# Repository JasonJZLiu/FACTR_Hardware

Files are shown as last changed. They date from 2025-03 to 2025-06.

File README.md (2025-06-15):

<h1> FACTR Low-Cost Force-Feedback Teleoperation Hardware</h1>

#### [Jason Jingzhou Liu](https://jasonjzliu.com)<sup>\*</sup>, [Yulong Li](https://yulongli42.github.io)<sup>\*</sup>, [Kenneth Shaw](https://kennyshaw.net), [Tony Tao](https://tony-tao.com), [Ruslan Salakhutdinov](https://www.cs.cmu.edu/~rsalakhu/), [Deepak Pathak](https://www.cs.cmu.edu/~dpathak/)
_Carnegie Mellon University_

[Project Page](https://jasonjzliu.com/factr/) | [arXiV](https://arxiv.org/abs/2502.17432) | [FACTR](https://github.com/RaindragonD/factr/) | [FACTR Teleop](https://github.com/RaindragonD/factr_teleop/)

<h1> </h1>
<div style="display: flex; gap: 10px; align-items: center;">
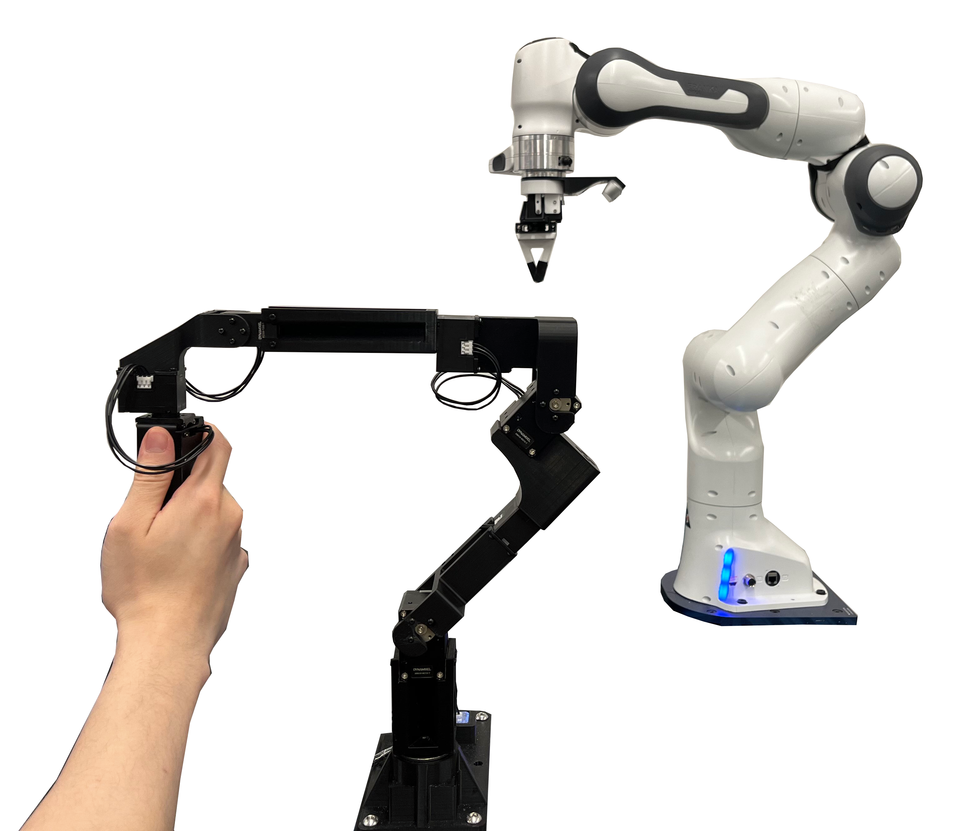
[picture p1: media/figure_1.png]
teaser_1
  
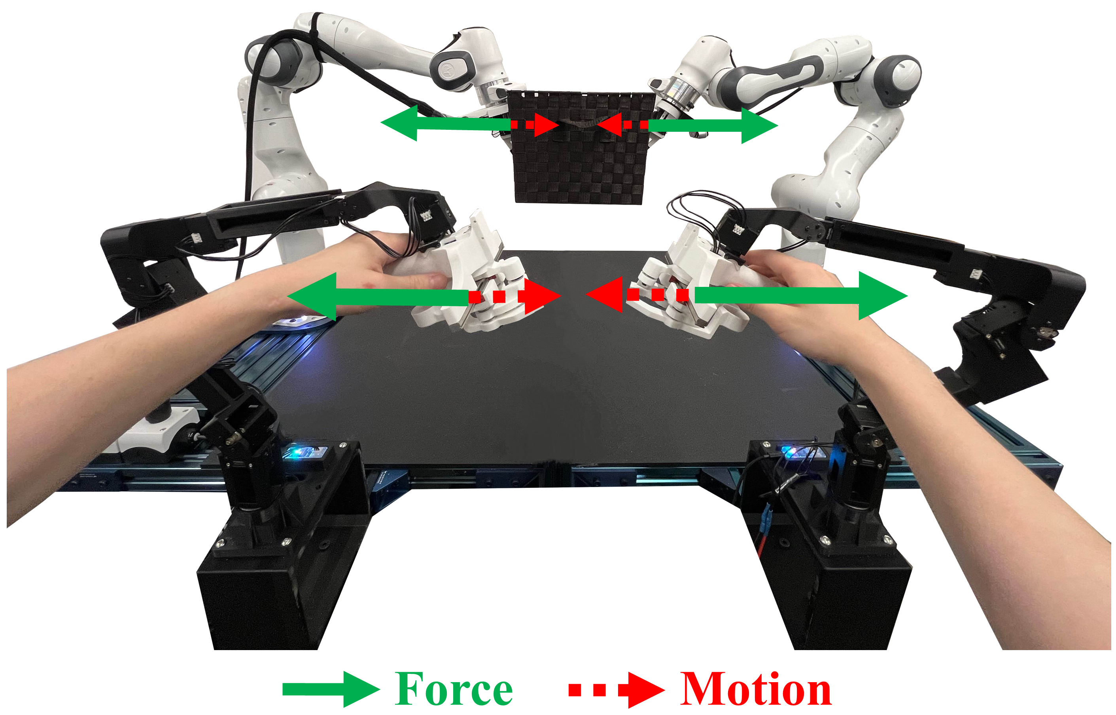
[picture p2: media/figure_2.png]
teaser_2
  
</div>

<br>

## Catalog
- [Bill of Materials](#bill-of-materials)
- [Building Instructions](#building-instructions)
- [License and Acknowledgements](#license-and-acknowledgements)
- [Citation](#citation)

## Bill of Materials
All costs are listed in USD.
<table>
  <thead>
    <tr>
      <th>Item</th>
      <th>Quantity</th>
      <th>Cost per Item</th>
      <th>Total Cost</th>
      <th>Note</th>
    </tr>
  </thead>
  <tbody>
    <tr>
      <td>Dynamixel XM430-W210-T Servo Motor</td>
      <td>2</td>
      <td>269.9</td>
      <td>539.8</td>
      <td><a href="https://www.robotis.us/dynamixel-xm430-w210-t/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">Purchase Link</a></td>
    </tr>
    <tr>
      <td>Dynamixel XC330-T288-T Servo Motor</td>
      <td>6</td>
      <td>89.9</td>
      <td>539.4</td>
      <td><a href="https://www.robotis.us/dynamixel-xc330-t288-t/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">Purchase Link</a></td>
    </tr>
    <tr>
      <td>U2D2 Control PCB</td>
      <td>1</td>
      <td>32.1</td>
      <td>32.1</td>
      <td><a href="https://www.robotis.us/u2d2/?srsltid=AfmBOopG82m7F47C2HJT4Q9btluaBp5lSfk2BS-57h5wBO3lwNoY3PoJ">Purchase Link</a></td>
    </tr>
    <tr>
      <td>12V 20A Power Supply</td>
      <td>1</td>
      <td>24.99</td>
      <td>24.99</td>
      <td><a href="https://www.amazon.com/ALITOVE-Transformer-Switching-Converter-Security/dp/B078RTV41D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">Purchase Link</a></td>
    </tr>
    <tr>
      <td>FPX330-S102 Servo Bracket</td>
      <td>1</td>
      <td>8.7</td>
      <td>8.7</td>
      <td><a href="https://www.robotis.us/fpx330-s102-4pcs-set/">Purchase Link</a></td>
    </tr>
    <tr>
      <td>Servo Idler for XM430 Servos</td>
      <td>2</td>
      <td>19.58</td>
      <td>39.16</td>
      <td><a href="https://www.robotis.us/hn12-i101-set/?srsltid=AfmBOooTVv1ehj551FepxB_NaPDrjRdgRIVPH26-N-vjoncqV3CZYdAC">Purchase Link</a></td>
    </tr>
    <tr>
      <td>Servo Idler for XC330 Servos</td>
      <td>1</td>
      <td>10.78</td>
      <td>10.78</td>
      <td><a href="https://www.robotis.us/fpx330-h101-4pcs-set/?srsltid=AfmBOopdWLnJLGadW4_-EK1PhWCb8sMwZvdChQUPqFrf1NNLNWeow4cJ">Purchase Link</a></td>
    </tr>
    <tr>
      <td>Polymaker PLA PRO Filament</td>
      <td>1</td>
      <td>24.99</td>
      <td>24.99</td>
      <td><a href="https://www.amazon.com/dp/B099KS2PDW?ref_=cm_sw_r_cp_ud_dp_9TYAHY4XBF45WRGQJGQ6">Purchase Link</a></td>
    </tr>
    <tr>
      <td>U2D2 Power Hub Board</td>
      <td>1</td>
      <td>19.99</td>
      <td>19.99</td>
      <td><a href="https://www.robotis.us/u2d2-power-hub-board-set/">Purchase Link</a></td>
    </tr>
    <tr>
      <td>14AWG Cable</td>
      <td>1</td>
      <td>23.99</td>
      <td>23.99</td>
      <td><a href="https://www.amazon.com/dp/B088RDY284?ref_=cm_sw_r_cp_ud_dp_4ESS07CK5QSXK185XQEP&th=1">Purchase Link</a></td>
    </tr>
    <tr>
      <td>3/4" Bearing</td>
      <td>1</td>
      <td>6.99</td>
      <td>6.99</td>
      <td><a href="https://www.amazon.com/4-Pack-Bearings-Carbon-Steel-Wheelbarrows/dp/B0CFDNP445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">Purchase Link</a></td>
    </tr>
    <tr>
      <td>M2.5×8mm</td>
      <td>8</td>
      <td>N/A</td>
      <td rowspan="3">15.99</td>
      <td rowspan="3"><a href="https://www.amazon.com/NINDEJIN-Replacement-Computer-Miniature-Motherboard/dp/B08KXS2MWG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">Purchase link</a></td>
    </tr>
    <tr>
      <td>M2×10mm</td>
      <td>20</td>
      <td>N/A</td>
    </tr>
    <tr>
      <td>M2×6mm</td>
      <td>14</td>
      <td>N/A</td>
    </tr>
    <tr>
      <td>M2×8mm (Self Tapping)</td>
      <td>24</td>
      <td>N/A</td>
      <td rowspan="2">0</td>
      <td rowspan="2">Comes with Dynamixel XC330-T288-T Servo Motor</td>
    </tr>
    <tr>
      <td>M2×6mm (Self Tapping)</td>
      <td>8</td>
      <td>N/A</td>
    </tr>
    <tr>
      <td>M2×4mm</td>
      <td>4</td>
      <td>N/A</td>
      <td>0</td>
      <td>Comes with FPX330-S102 Servo Bracket</td>
    </tr>
    <tr>
      <td colspan="3"><b>Total</b></td>
      <td colspan="2"><b>1279.89</b></td>
    </tr>
  </tbody>
</table>

## Building Instructions

### Screw Guide

The FACTR Teleoperation Franka Leader Arm assembly requires six types of screws:

- **Screw A**: M2.5 × 8 mm  
- **Screw B**: M2 × 10 mm  
- **Screw C**: M2 × 8 mm (Self-tapping)  
- **Screw D**: M2 × 6 mm (Self-tapping)  
- **Screw E**: M2 × 6 mm  
- **Screw F**: M2 × 4 mm  

**Note:**  
- Screws **C** and **D** are included with the *Dynamixel XC330-T288-T* servos.  
- Screw **F** is included with the *FPX330-S102* servo bracket.

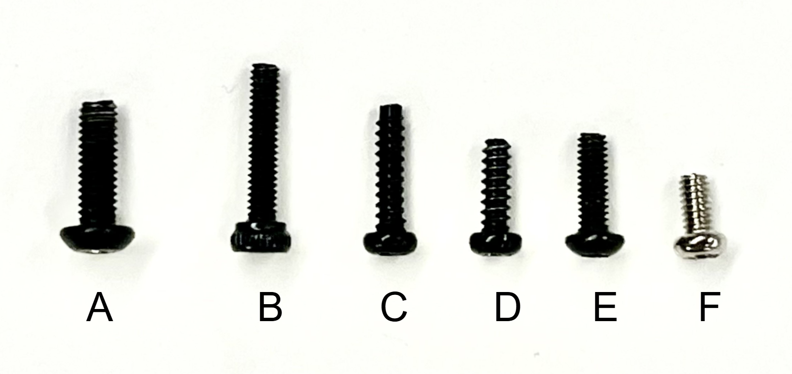
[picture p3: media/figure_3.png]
Screw Guide


---

### Step 1: Configure the Power Supply
- Connect the **12V Power Supply** to the **U2D2 Power Hub Board**.  
- Connect the **U2D2 Control PCB** to the **U2D2 Power Hub Board**.

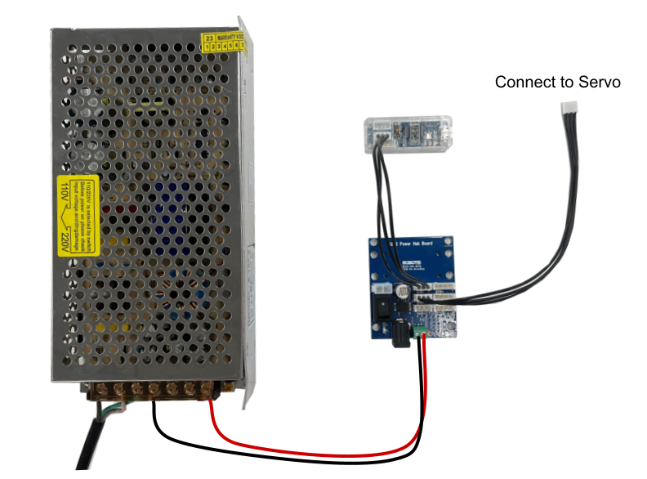
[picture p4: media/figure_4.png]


**Note:** Alternative ways of supplying power to the **U2D2 Control PCB** and the servos without using **U2D2 Power Hub Board** are available. 
Please refer to [here](https://emanual.robotis.com/docs/en/parts/interface/u2d2/) for more methods.

### Step 2: Update Servo IDs
By default, all Dynamixel servos are set to ID 1. To control multiple servos with a single U2D2 controller, 
each servo must be assigned a unique ID. This assignment should be done one servo at a time, starting with 
the servo closest to the robot base and progressing up the kinematic chain. Assign IDs sequentially from 
1 up to 8, with the gripper trigger servo holding ID 8. 

| Joint ID | Servo Type |
|---|---|
| 1 | Dynamixel XC330-T288-T |
| 2 | Dynamixel XM430-W210-T |
| 3 | Dynamixel XC330-T288-T |
| 4 | Dynamixel XM430-W210-T |
| 5 | Dynamixel XC330-T288-T |
| 6 | Dynamixel XC330-T288-T |
| 7 | Dynamixel XC330-T288-T |
| 8 | Dynamixel XC330-T288-T |

#### Steps to Change a Servo's ID:
1. **Connect a single servo to the U2D2 Power Hub Board.**
2. **Install and launch the [Dynamixel Wizard](https://emanual.robotis.com/docs/en/software/dynamixel/dynamixel_wizard2/) software.**
3. **Configure the scanning settings:**
   - In the top menu bar, go to **Tools → Options**.
   - Under **"Select port to scan"**, ensure all ports are selected.
   - Under **"Select baudrate to scan"**, choose the correct baudrate. The default is **57600 bps**. If unsure, select all available options.
   - Under **"Set ID range to scan"**, you can speed up scanning by limiting the range to **0–15**, unless the servo might already have an ID outside this range.
4. **Click the Scan icon** (magnifying glass with a gear) in the top-left corner.
   - If the servo is found, it will appear in the left panel of the window.
5. **Select the detected servo** from the panel, then click **ID** found in the middle panel of the window.
   - Select the new ID on the right panel of the window and click **Save**.
6. **Repeat** the above steps for each servo.

### Step 3: 3D Print the Body Links of the Leader Arm
The leader arm consists of **nine 3D-printed parts**. STL files for all components can be found in the `/3D_printing_files` directory.

- **Material**: PLA  
- **Infill**: 20%

To ensure accurate dynamic modeling, each printed part should closely match the specified mass values. These values correspond to the mass values 
defined in the provided URDF file. This URDF file is used to compute gravity compensation and other dynamics-related calculations.

The table below lists each part, its corresponding STL file, and its reference mass:

| Part Name | STL File | Mass (g) |
|---|---|---|
| Base Link | factr_teleop_franka_base.STL | 150 |
| Link 1 | factr_teleop_franka_l1.STL | 31 |
| Link 2 | factr_teleop_franka_l2.STL | 19 |
| Link 3 | factr_teleop_franka_l3.STL | 29 |
| Link 4 | factr_teleop_franka_l4.STL | 28 |
| Link 5 | factr_teleop_franka_l5.STL | 25 |
| Link 6 | factr_teleop_franka_l6.STL | 12 |
| Gripper Handle | factr_teleop_gripper_leader_handle.STL | 21 |
| Gripper Trigger | factr_teleop_gripper_trigger.STL | 5 |
| 3/4" Bearing | N/A | 39 |
| Dynamixel XM430-W210-T | N/A | 84 |
| Dynamixel XC330-T288-T | N/A | 23 |

### Step 4: Assemble the FACTR Teleop Franka Leader Arm
Follow the instructions below to assemble the leader arm, starting from the **base link** and progressing up to the **gripper teleoperation device**.

#### Base Link
Secure the **U2D2 Power Hub Board** on the **Base Link** and insert the **Bearing** as follows. 

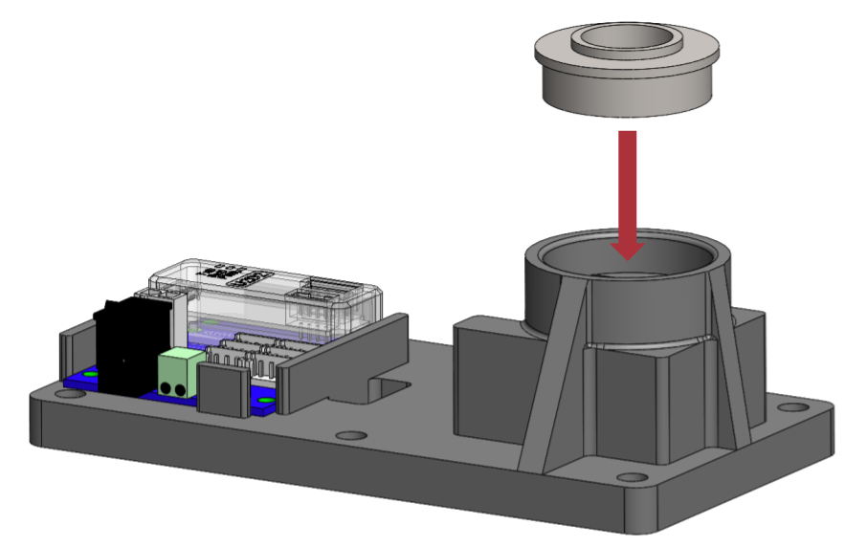
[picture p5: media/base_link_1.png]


Slide **Servo 1** such that its servo horn is concentric with the **Bearing**.

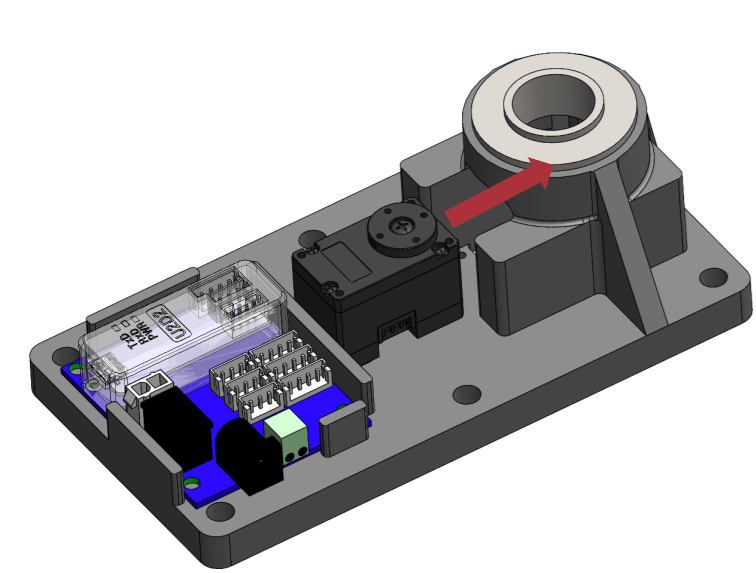
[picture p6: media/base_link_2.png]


On the under-side of the **Base Link**, secure **Servo 1** with four **Screw B** screws. Connect **Servo 1** to the **U2D2 Power Hub Board**. 

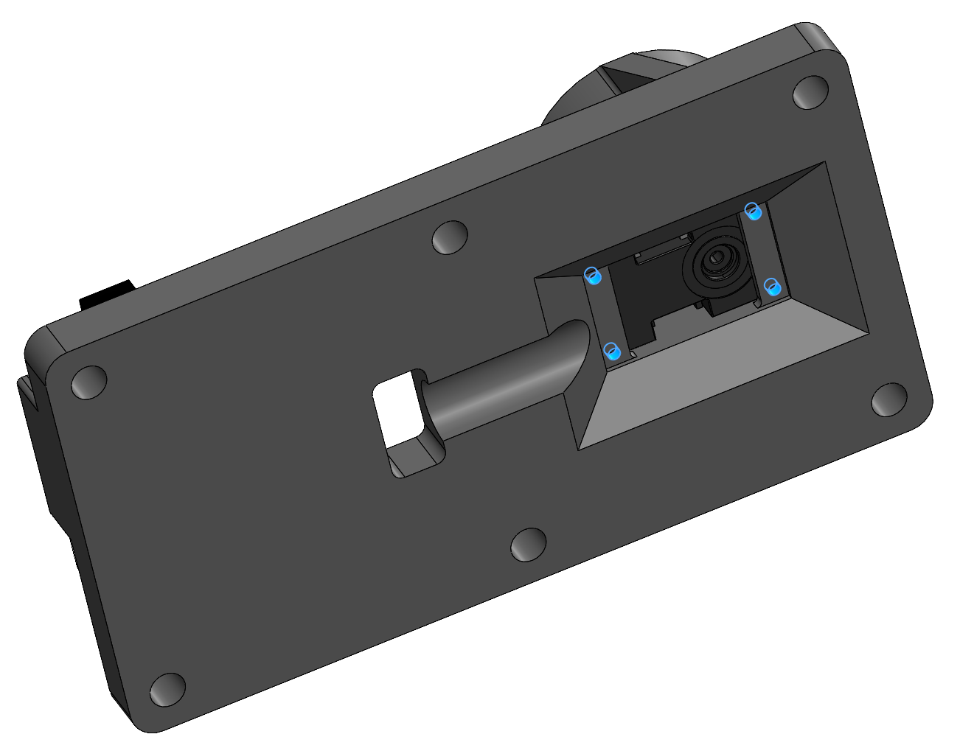
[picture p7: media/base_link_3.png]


#### Link 1
Insert **Link 1** fully into the bearing hole. Secure **Link 1** onto the servo horn of **Servo 1** using four **Screw C** screws.

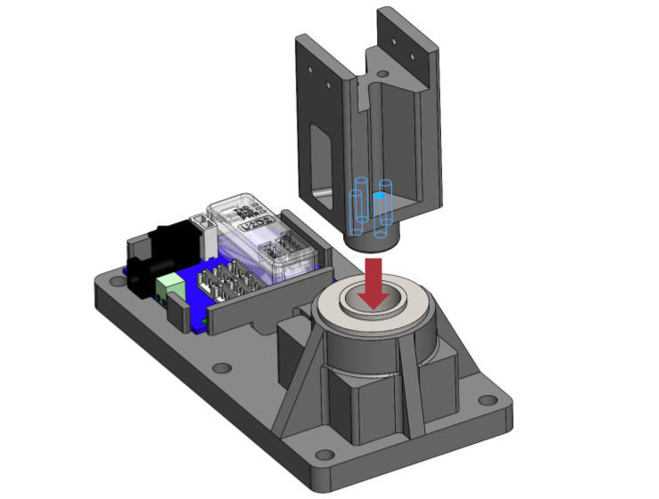
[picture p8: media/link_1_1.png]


Secure **Servo 2** onto **Link 1** using four **Screw A** screws. Connect **Servo 2** to the **U2D2 Power Hub Board**.

**Note:** For the purpose of this assembly tutorial, ensure the orientation of **Servo 2** matches that of the provided images,
where the side of the servo horn is facing the viewer. On the other side of **Servo 2**, also ensure that **Servo 2**'s idler is installed. 

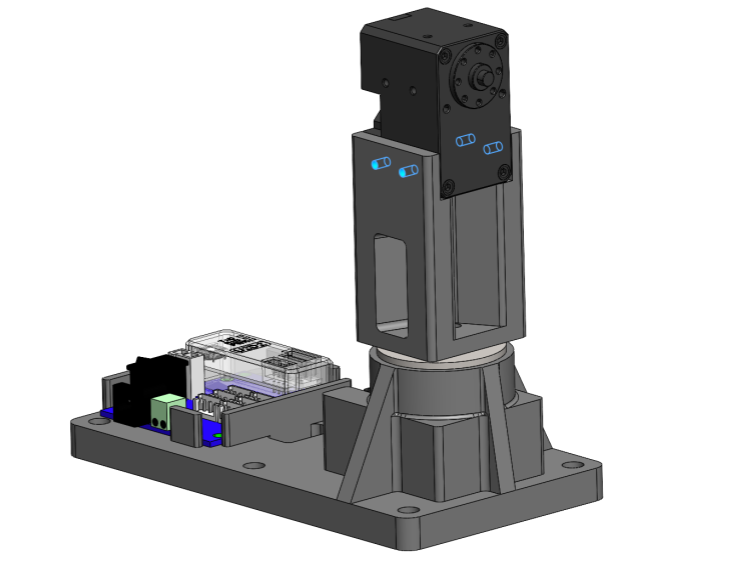
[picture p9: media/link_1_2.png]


#### Link 2
Slide **Link 2** onto the servo horn of **Servo 2** and secure it via seven **Screw E** screws.

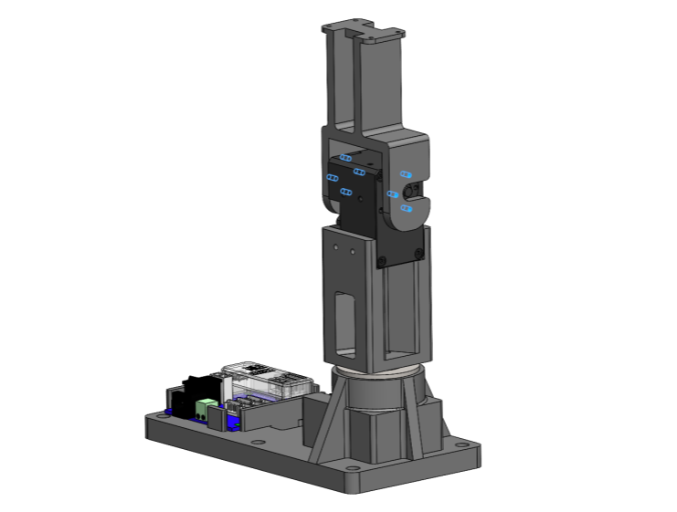
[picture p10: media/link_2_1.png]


Secure **Servo 3** onto **Link 2** with four **Screw B** screws. Connect **Servo 3** to **Servo 2**.

**Note:** Please ensure the orientation of the servo matches the image shown below.

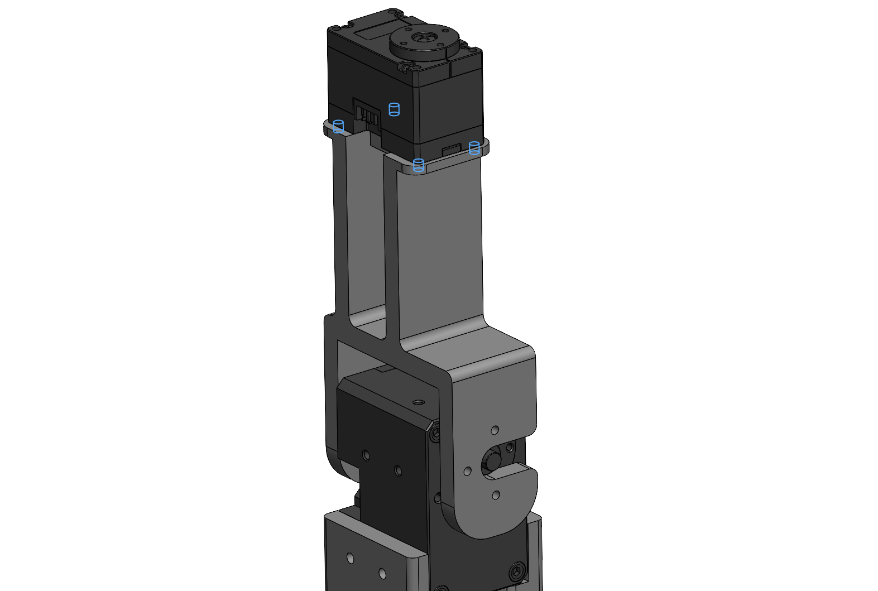
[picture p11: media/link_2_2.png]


#### Link 3
Secure **Link 3** onto the servo horn of **Servo 3** using four **Screw C** screws.

**Note:** If you choose to increase the force-feedback gain to enhance the force-feedback sensation, 
consider replacing **Servo 3**'s plastic servo horn to a 
[metal version](https://www.robotis.us/hnx330-n101-set/?srsltid=AfmBOop3pO_EHjoTXnjaf3ZWbRD_CDD0ClY2xiPG_qw5SiEay-YZPcLH).
The default plastic horn may be prone to failure under higher loads.
 
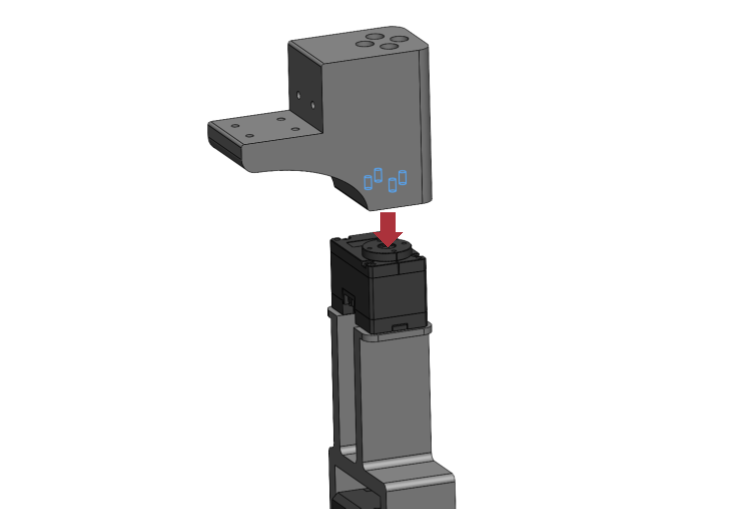
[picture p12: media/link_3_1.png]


Secure **Servo 4** onto **Link 3** using four **Screw A** screws. Ensure **Servo 4**'s idler is installed.
Connect **Servo 4** to **Servo 3**.

**Note:** Please ensure the orientation of the servo matches the image shown below, with the side of te servo horn facing the viewer.

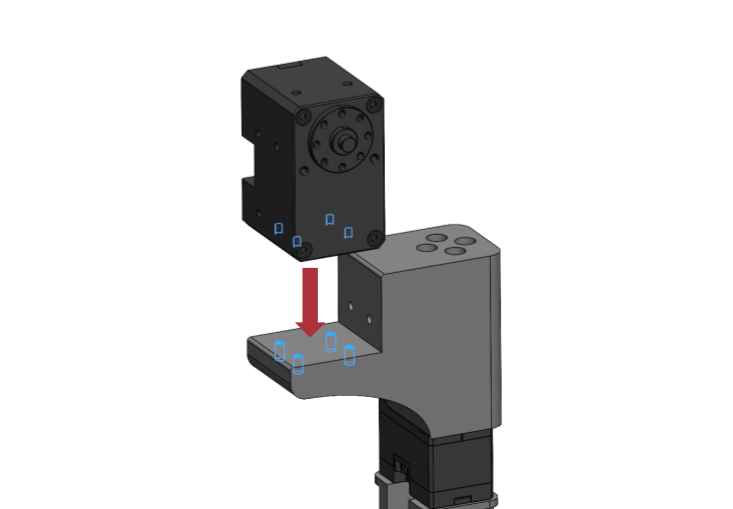
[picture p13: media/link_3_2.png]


#### Link 4
Slide **Link 4** onto the servo horn of **Servo 4** and secure it via seven **Screw E** screws.

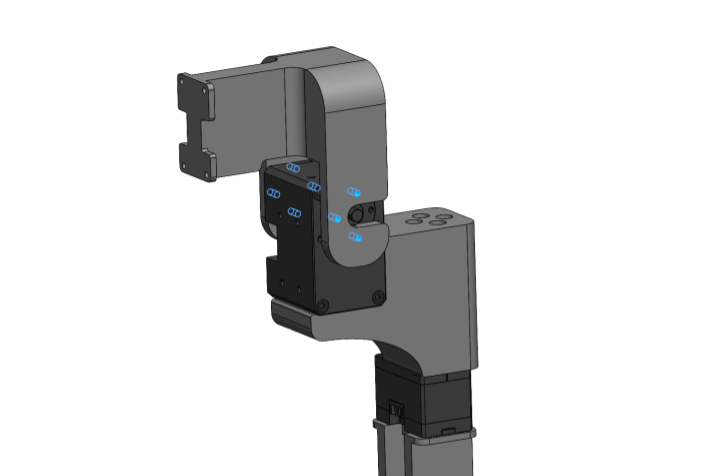
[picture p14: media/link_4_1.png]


Secure **Servo 5** onto the **Link 4** using four **Screw B** screws. Connect **Servo 5** to **Servo 4**.

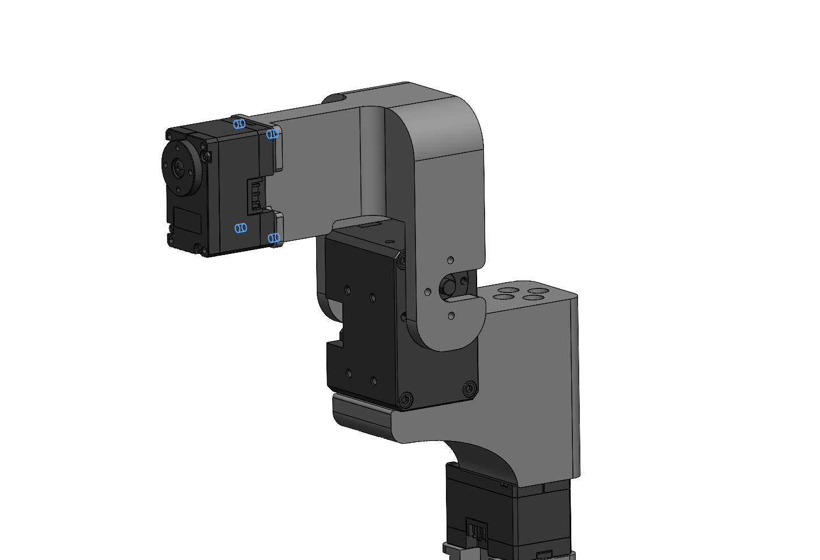
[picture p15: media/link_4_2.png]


#### Link 5
Secure **Link 5** onto the servo horn of **Servo 5** using four **Screw C** screws.

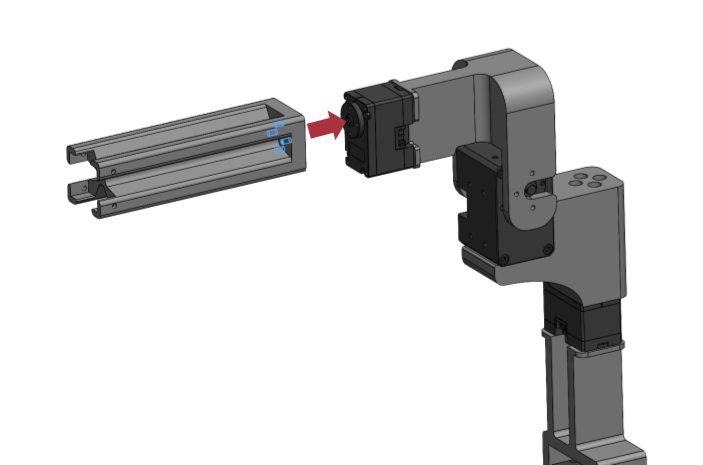
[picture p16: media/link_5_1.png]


Secure **Servo 6** onto **Link 5** Using four **Screw B** screws. Install **Servo 6**'s idler. Connect
**Servo 6** to **Servo 5**.

**Note:** Please ensure the orientation of the servo matches the image shown below, with the side of te servo horn facing the viewer
and its idler facing away from the viewer.

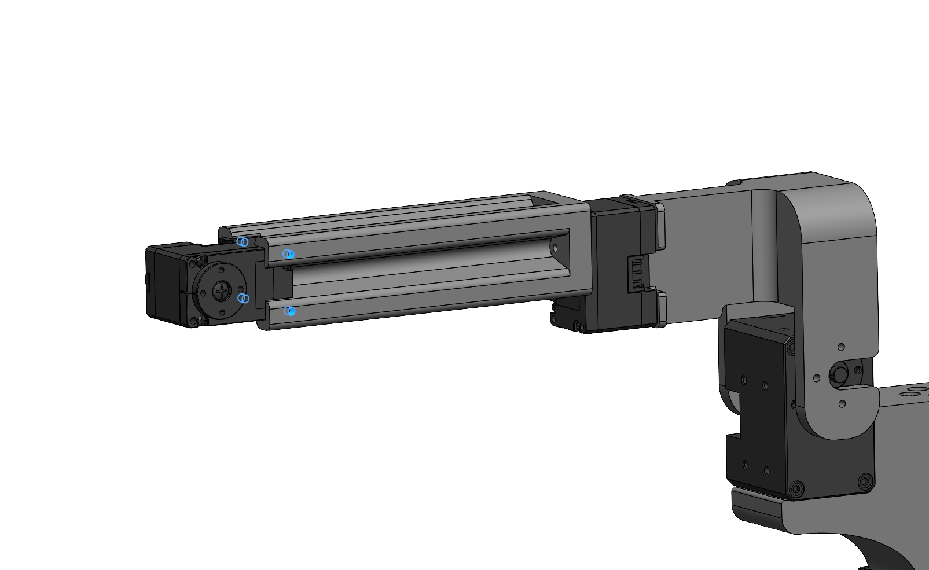
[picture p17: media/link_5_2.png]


#### Link 6
Slide **Link 6** onto the servo horn of **Servo 6** and secure it using eight **Screw D** screws.

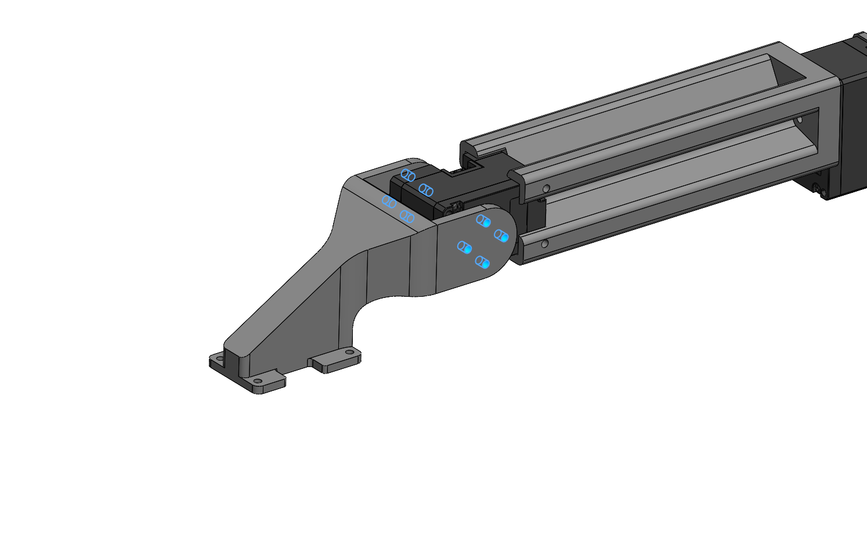
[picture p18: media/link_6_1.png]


Secure **Servo 7** onto **Link 6** using four **Screw B** screws. Connect **Servo 7** to **Servo 6**.

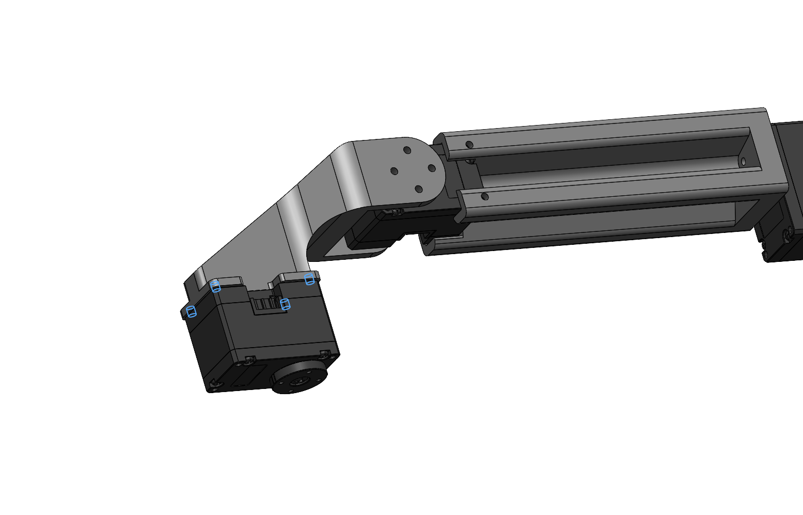
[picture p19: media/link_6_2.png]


Secure **Servo Bracket** onto the servo horn of **Servo 7** using four **Screw F** screws.

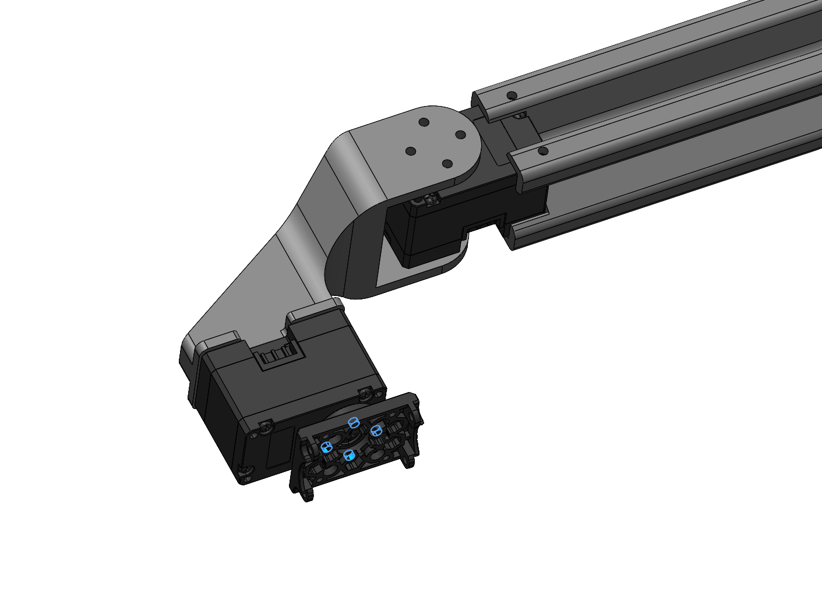
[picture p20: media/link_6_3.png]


#### Gripper Teleop Leader
Secure **Gripper Handle** onto **Servo Bracket** using four **Screw C** screws.

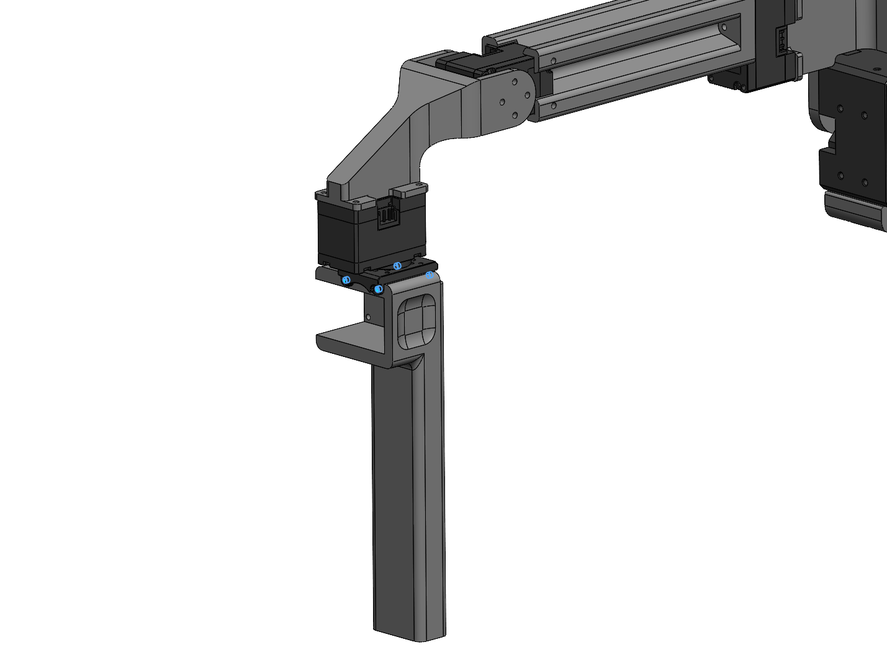
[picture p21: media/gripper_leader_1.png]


Slide **Servo 8** into **Gripper Handle** and secure it from the back using four **Screw C** screws.
Connect **Servo 8** to **Servo 7**.

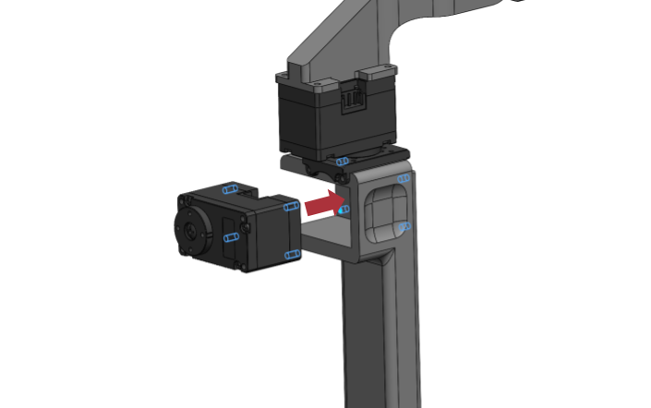
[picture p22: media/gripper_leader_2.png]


Secure **Gripper Trigger** onto the servo horn of **Servo 8** using four **Screw C** screws.

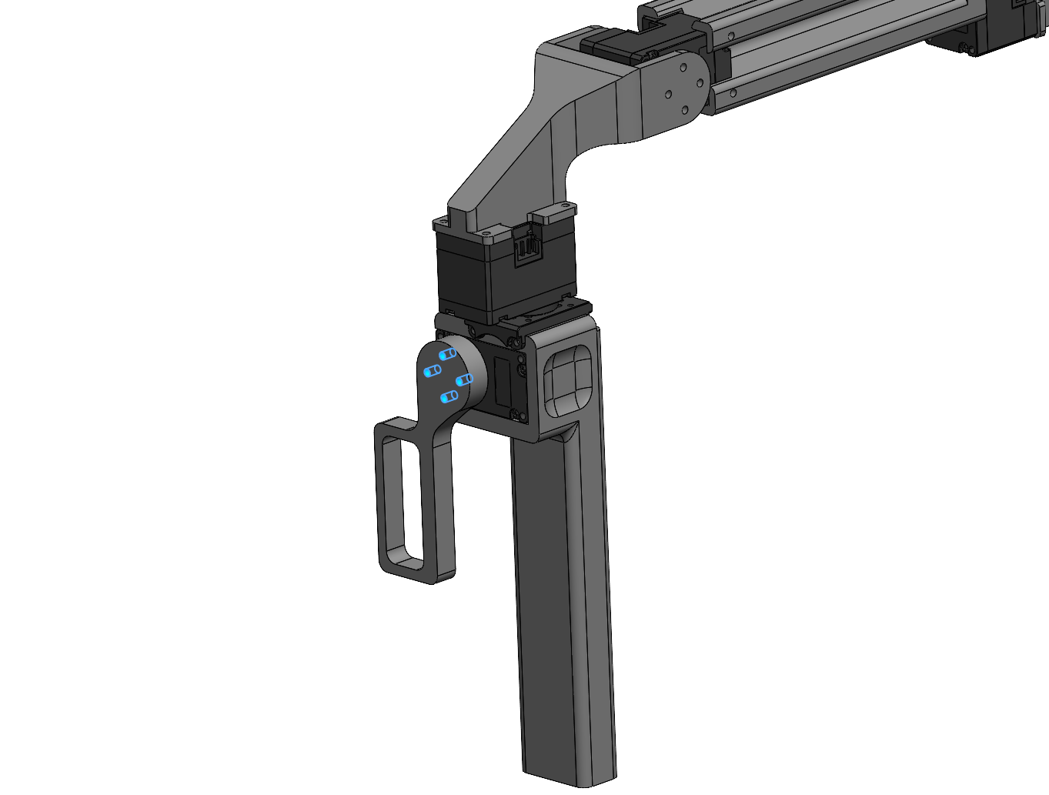
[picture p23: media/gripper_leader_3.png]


**Note:** The gripper teleoperation leader presented here is a simplified and lighter update 
of the version shown in the figures of the paper.

#### Finished Assembly
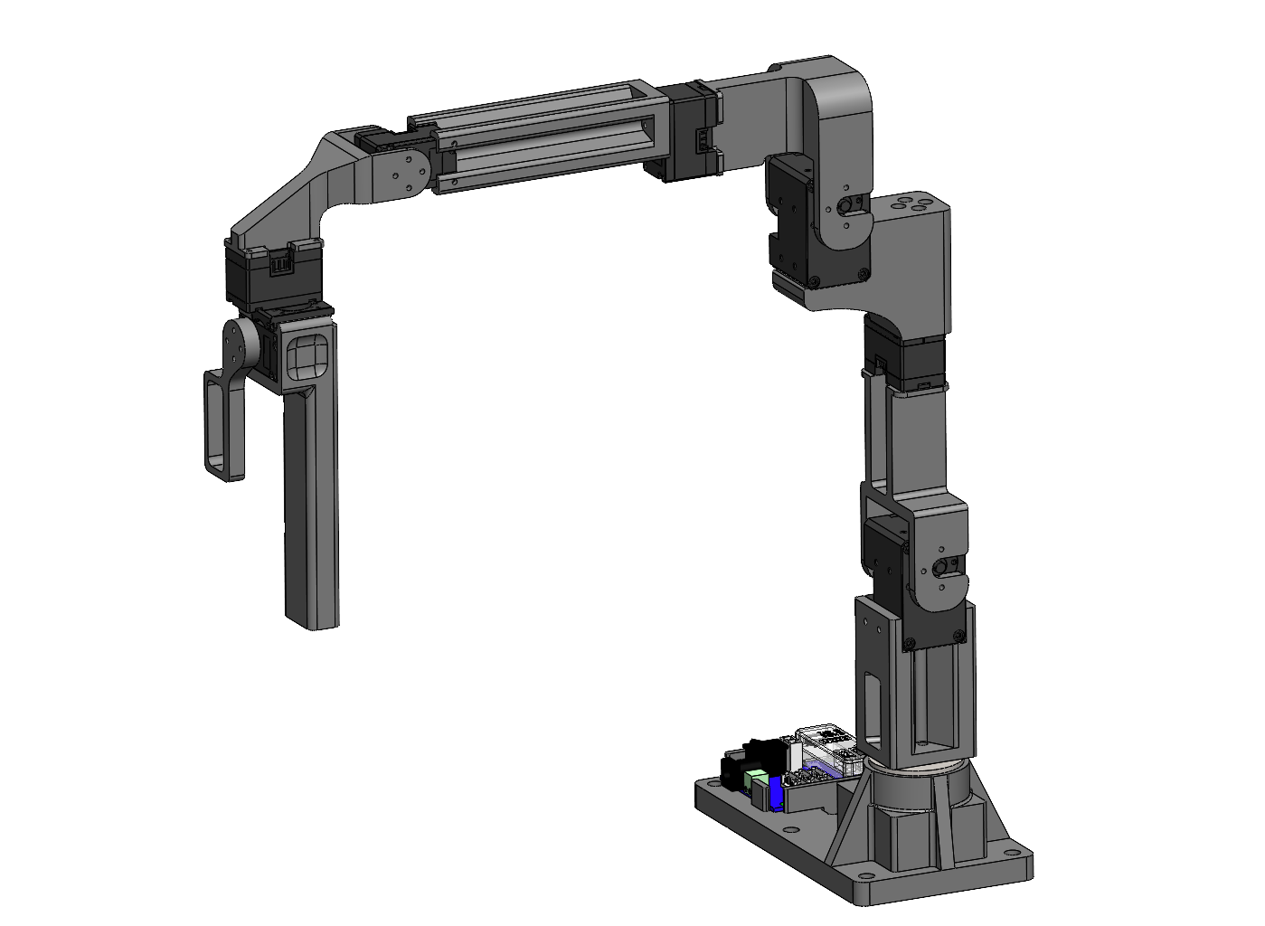
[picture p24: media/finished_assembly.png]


## License and Acknowledgements
This source code is licensed under the Apache 2.0 liscence found in the LICENSE file in the root directory of this repository.

Special thanks to the [GELLO](https://wuphilipp.github.io/gello_site/) project for serving as a source of inspiration for this work.

## Citation
If you find this project useful, feel free to cite our work!
<div style="display:flex;">
<div>

```bibtex
@article{factr,
  title={FACTR: Force-Attending Curriculum Training for Contact-Rich Policy Learning},
  author={Liu, Jason Jingzhou and Li, Yulong and Shaw, Kenneth and Tao, Tony and Salakhutdinov, Ruslan and Pathak, Deepak},
  journal={arXiv preprint arXiv:2502.17432},
  year={2025}
}
```

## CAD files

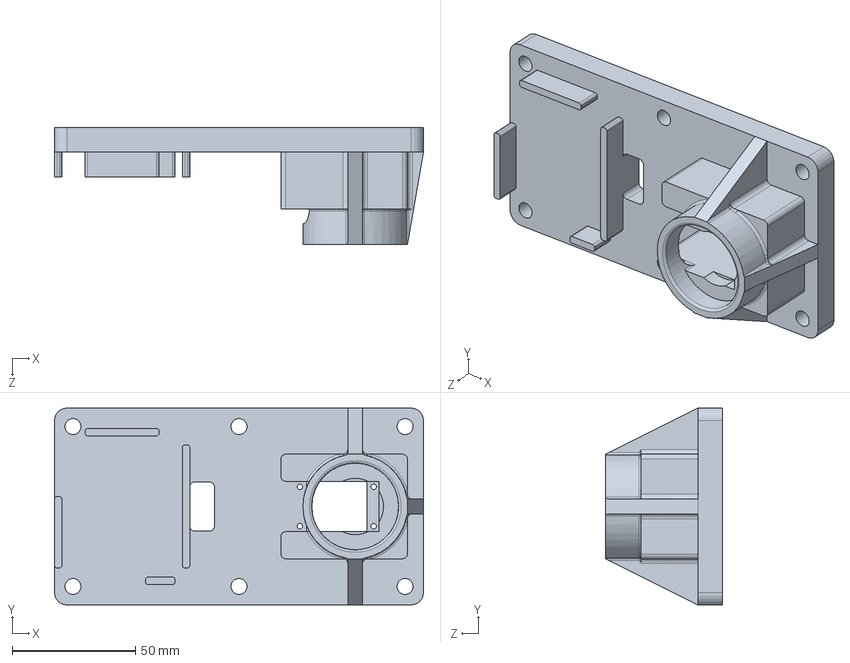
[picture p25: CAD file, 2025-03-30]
CAD_files/SOLIDWORKS_files/base/factr_teleop_franka_base.SLDPRT
150.0 x 80.0 x 47.5 mm

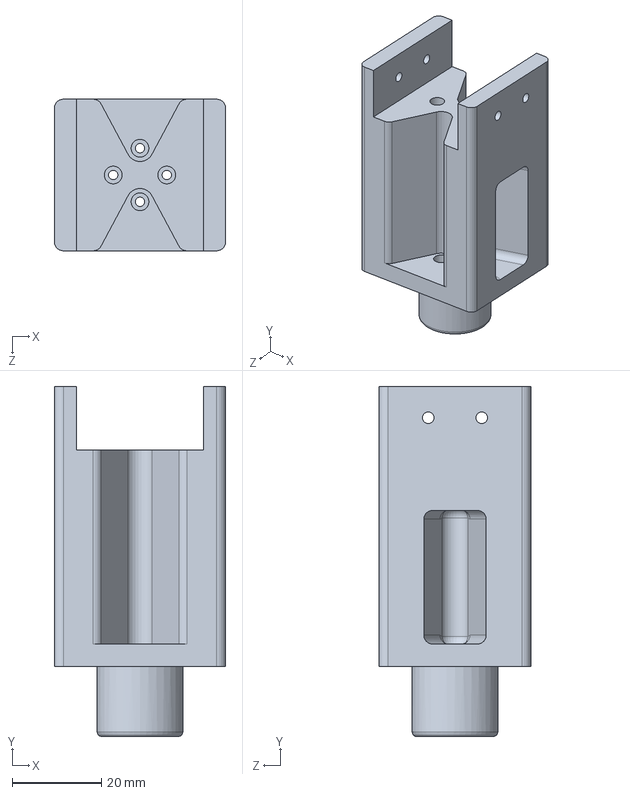
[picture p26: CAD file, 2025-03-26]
CAD_files/SOLIDWORKS_files/l1/factr_teleop_franka_l1.SLDPRT
38.4 x 78.5 x 34.0 mm

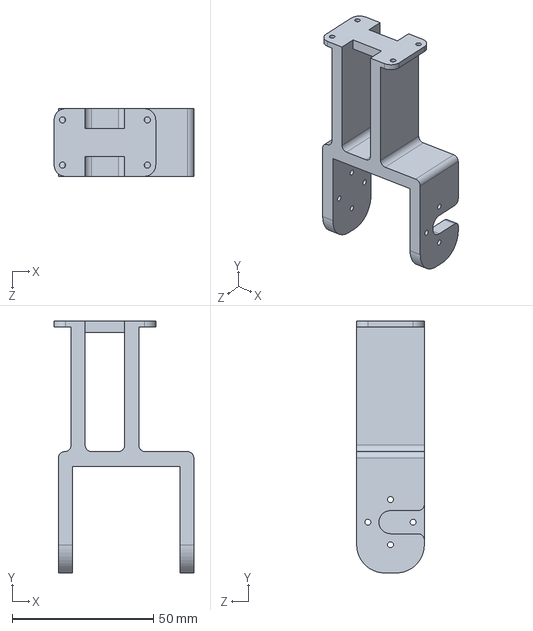
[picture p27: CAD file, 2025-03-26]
CAD_files/SOLIDWORKS_files/l2/factr_teleop_franka_l2.SLDPRT
49.5 x 89.2 x 24.0 mm

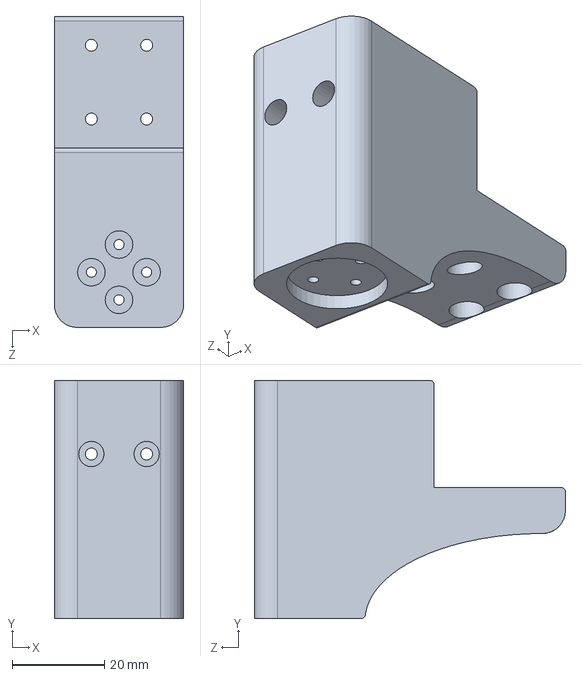
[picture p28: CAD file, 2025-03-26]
CAD_files/SOLIDWORKS_files/l3/factr_teleop_franka_l3.SLDPRT
28.1 x 51.7 x 67.5 mm

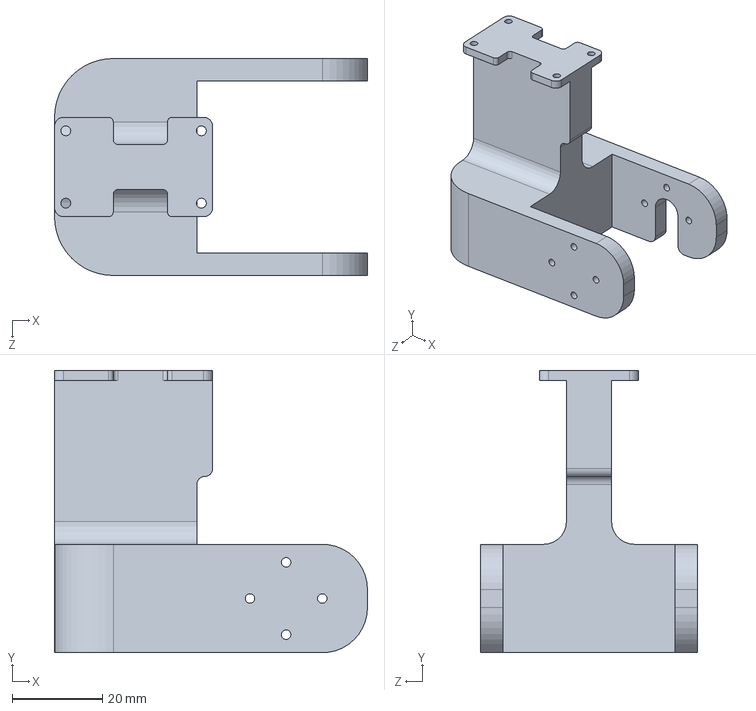
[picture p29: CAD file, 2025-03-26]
CAD_files/SOLIDWORKS_files/l4/factr_teleop_franka_l4.SLDPRT
69.2 x 62.5 x 48.0 mm

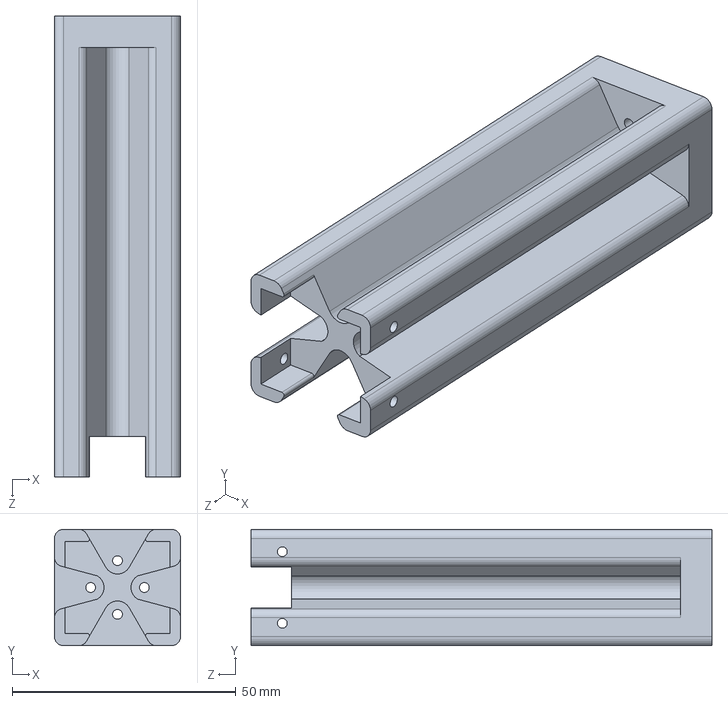
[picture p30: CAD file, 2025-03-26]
CAD_files/SOLIDWORKS_files/l5/factr_teleop_franka_l5.SLDPRT
28.2 x 26.0 x 103.0 mm

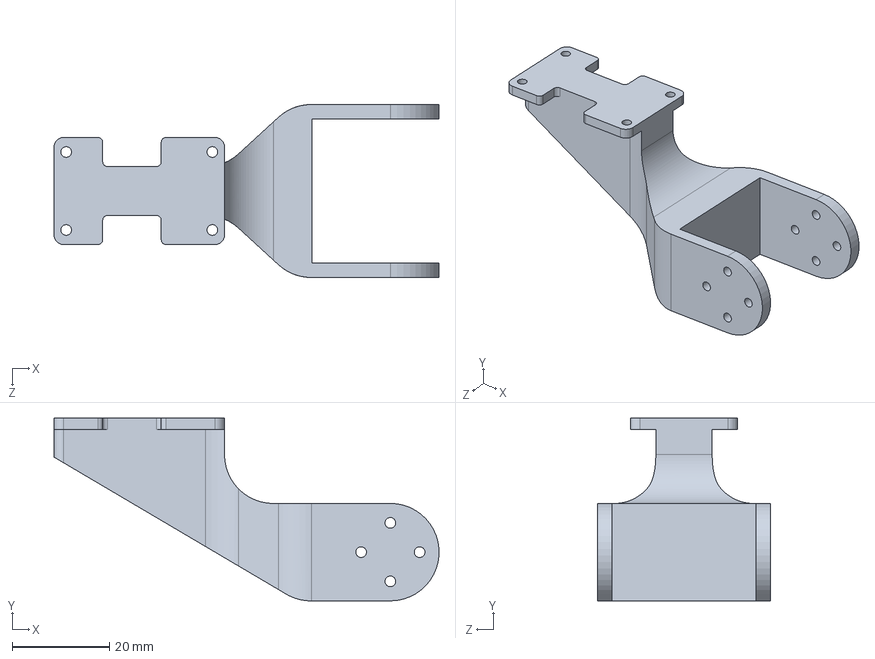
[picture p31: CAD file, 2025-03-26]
CAD_files/SOLIDWORKS_files/l6/factr_teleop_franka_l6.SLDPRT
79.0 x 37.5 x 35.5 mm

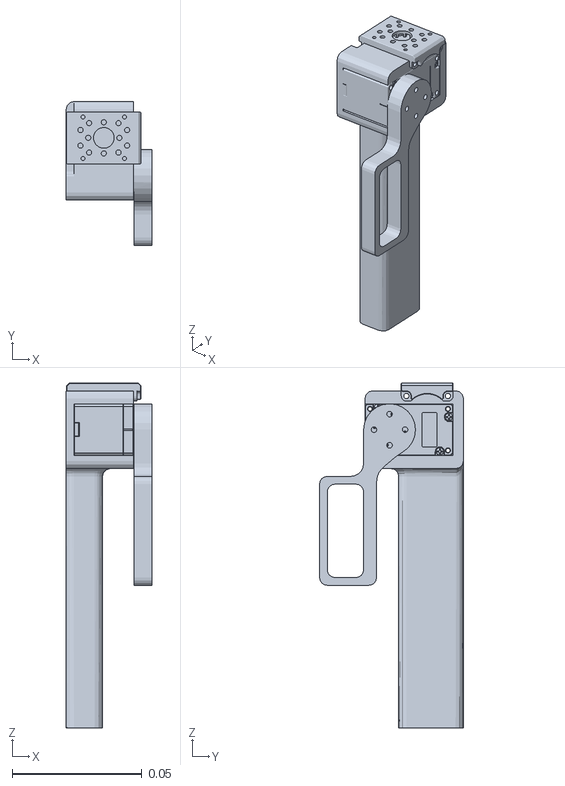
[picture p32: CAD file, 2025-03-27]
urdf/meshes/link_7.STL
0.033 x 0.0555 x 0.133

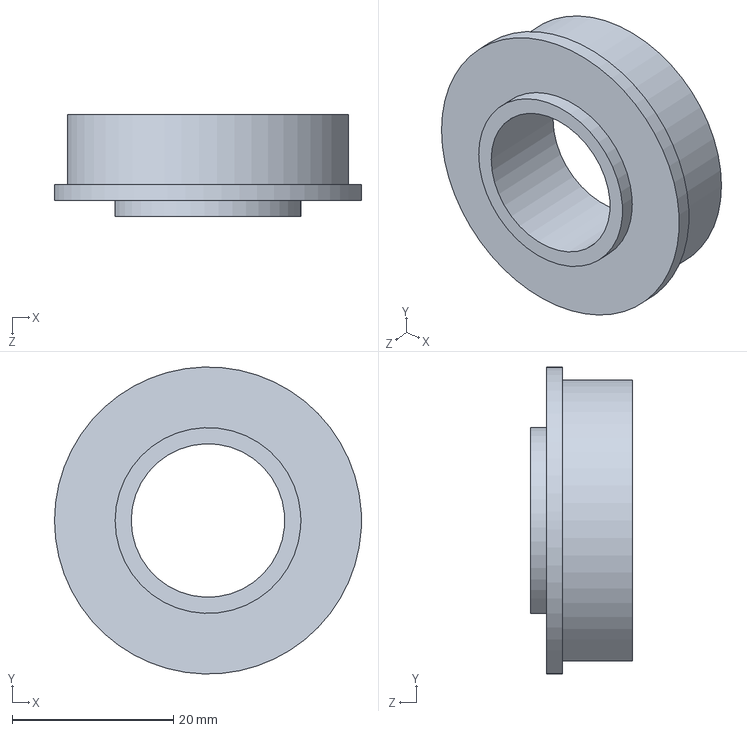
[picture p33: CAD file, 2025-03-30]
CAD_files/SOLIDWORKS_files/base/factr_teleop_base_bearing.SLDPRT
38.1 x 38.1 x 12.7 mm

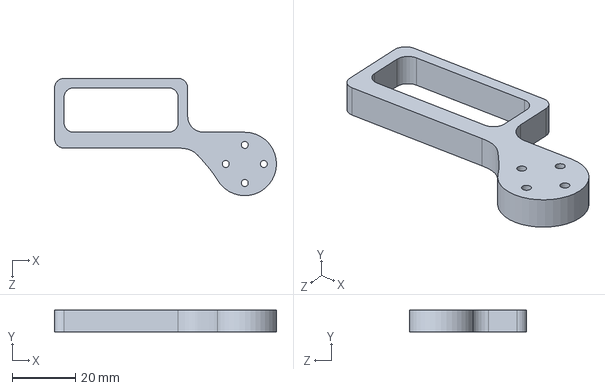
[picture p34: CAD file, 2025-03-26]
CAD_files/SOLIDWORKS_files/gripper_leader/factr_teleop_gripper_trigger.SLDPRT
70.0 x 6.90 x 37.0 mm

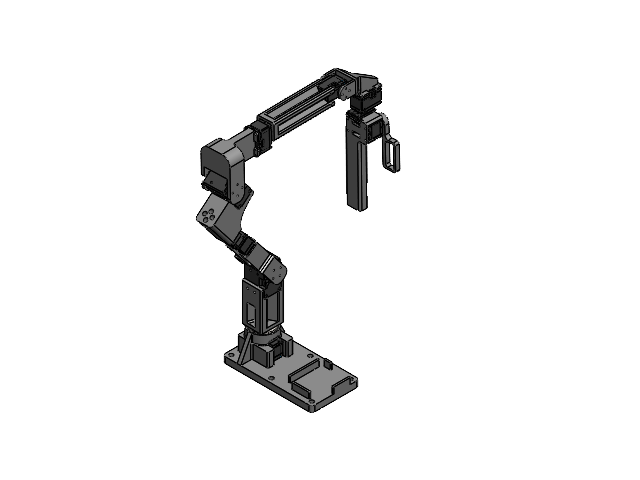
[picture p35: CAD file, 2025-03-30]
CAD_files/SOLIDWORKS_files/FACTR_teleop_franka.SLDASM
factr_teleop_franka_base
factr_teleop_base_bearing
DC15_A01_CASE_M_DUMMY.stp x 6
DC15_A01_CASE_F_DUMMY.stp x 6
DC15_A01_CASE_B_DUMMY.stp x 6
DC15_A01_HORN_DUMMY.stp x 6
DC15_A01_LED_CAP2_DUMMY.stp x 6
PHS_1_7X20_5_DC10.stp x 24
BTS2_M2_6X8.stp x 12
DC15_A01_IDLE_CAP_DUMMY.stp x 6
B3B-EH.stp x 12
factr_teleop_franka_l1
DUMMY_DC12.stp x 2
WBH_M2_5X12.stp x 16
DC12_A01_SPACER_RING_1.stp x 16
factr_teleop_franka_l2
factr_teleop_franka_l3
factr_teleop_franka_l4
factr_teleop_franka_l5
factr_teleop_franka_l6
XM330_motor_frame
factr_teleop_gripper_leader_handle
factr_teleop_gripper_trigger

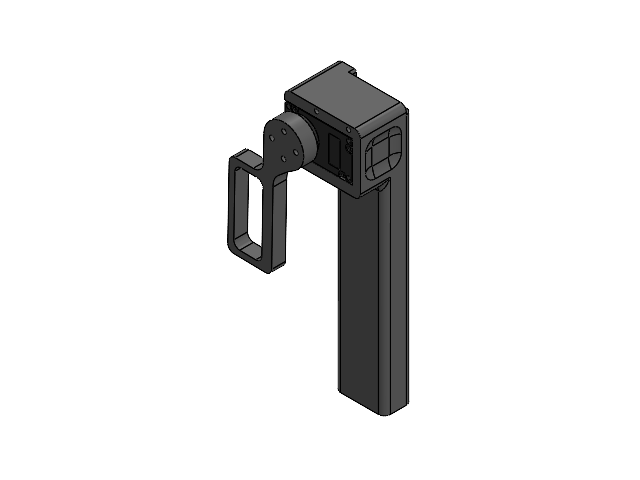
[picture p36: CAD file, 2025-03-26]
CAD_files/SOLIDWORKS_files/gripper_leader/factr_teleop_gripper_leader.SLDASM
factr_teleop_gripper_leader_handle
DC15_A01_CASE_M_DUMMY.stp
DC15_A01_CASE_F_DUMMY.stp
DC15_A01_CASE_B_DUMMY.stp
DC15_A01_HORN_DUMMY.stp
DC15_A01_LED_CAP2_DUMMY.stp
PHS_1_7X20_5_DC10.stp x 4
BTS2_M2_6X8.stp
B3B-EH.stp x 2
factr_teleop_gripper_trigger

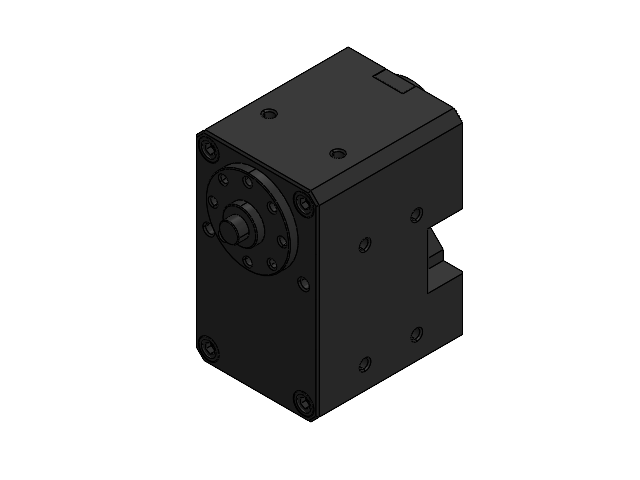
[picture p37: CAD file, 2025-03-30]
CAD_files/SOLIDWORKS_files/motor/XM430.SLDASM
DUMMY_DC12.stp
WBH_M2_5X12.stp x 8
DC12_A01_SPACER_RING_1.stp x 8

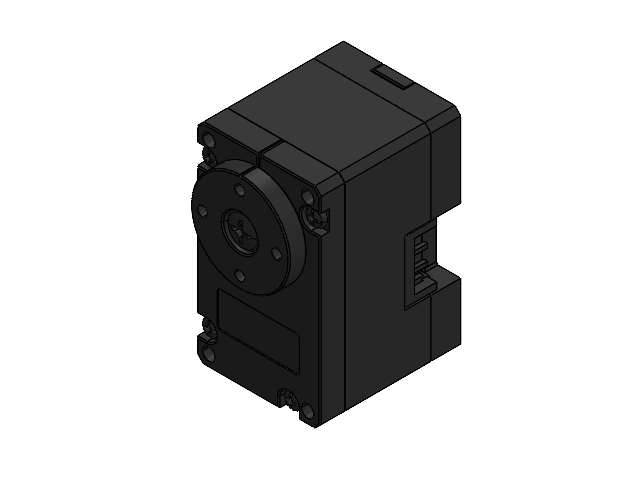
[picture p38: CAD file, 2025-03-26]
CAD_files/SOLIDWORKS_files/motor/XM330_no_idler.SLDASM
DC15_A01_CASE_M_DUMMY.stp
DC15_A01_CASE_F_DUMMY.stp
DC15_A01_CASE_B_DUMMY.stp
DC15_A01_HORN_DUMMY.stp
DC15_A01_LED_CAP2_DUMMY.stp
PHS_1_7X20_5_DC10.stp x 4
BTS2_M2_6X8.stp
B3B-EH.stp x 2

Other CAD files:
CAD_files/SOLIDWORKS_files/base/U2D2_power_hub_board.SLDASM
CAD_files/SOLIDWORKS_files/motor/XM330.SLDASM
CAD_files/STEP_files/factr_teleop_franka_l6.STEP
CAD_files/STEP_files/factr_teleop_franka_l5.STEP
3D_printing_files/factr_teleop_franka_base.STL
3D_printing_files/factr_teleop_franka_l1.STL
3D_printing_files/factr_teleop_franka_l2.STL
3D_printing_files/factr_teleop_franka_l3.STL
3D_printing_files/factr_teleop_franka_l4.STL
3D_printing_files/factr_teleop_franka_l5.STL
3D_printing_files/factr_teleop_franka_l6.STL
3D_printing_files/factr_teleop_gripper_leader_handle.STL
3D_printing_files/factr_teleop_gripper_trigger.STL
CAD_files/SOLIDWORKS_files/gripper_leader/factr_teleop_gripper_leader_handle.SLDPRT
CAD_files/SOLIDWORKS_files/motor/XM330_motor_frame.SLDPRT
CAD_files/STEP_files/factr_teleop_franka_base.STEP
CAD_files/STEP_files/factr_teleop_franka_l1.STEP
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

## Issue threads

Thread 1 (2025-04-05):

Gripper attached on the FER

danielsanjosepro, 2025-04-05:
Hey!

Amazing design, I really appreciate your work. I was looking around but I could not find the gripper attached to the FER. It looks like you designed it yourself as well. Have you also open-sourced it ? thanks in advance!

Best,
Daniel

JasonJZLiu, 2025-04-08:
Hi Daniel,

Thanks for the support! The gripper we used was actually just the default gripper from the [OpenManipulator-X arm](https://www.robotis.us/openmanipulator-x-rm-x52-tnm/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), but any other gripper should also work.

Best,
Jason

danielsanjosepro, 2025-04-09:
Alright, sound great. Have you then designed an adapter for the franka emika robot?
